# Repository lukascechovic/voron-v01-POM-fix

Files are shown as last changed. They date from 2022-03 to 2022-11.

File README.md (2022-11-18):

# voron-v01-POM-fix
**Issue: Z motor is binding/skipping at default 0.37A current with empty bed, with properly aligned parts (Z leadscrew and  POM nut T8_Nut_Block plastic part)**
[Youtube Video](https://youtu.be/tI24zk7298Q )

Originally used for LDO v0.1 kit rev C Anti Backlash Nut, POM, Tr8X8, if you got Z binding-skipping on default Z motor current 0.37A, with good Z axis alignment

hm.. increase in Z motor amps to 0.5A-0.55A solve this but at the cost of grinding plastic POM down and potentialy harm other parts of printer (head) as you really dont wanna super strong Z power (imagine Z endstop wont trigger)

**My best practice of aligning Z - before we hop into more unpleasant stuff**
1. fix Z motor (tighten all 4 screws) , bear in mind that you should trigger Z endstop with screw in T8_Nut_Block plastic part, for me it was more on rigth side from front view, POM nut is already on leadscrew
2. fix POM nut in T8_Nut_Block plastic part (tighten 2 screws), while T8_Nut_Block itself is still losen on alu Z profile
3. bring bed down (rotate leadscrew by hand), align T8_Nut_Block plastic part with leadscrew and tighten it (if you have backplate on, there are drilled two holes for wrench)
4. if you are lucky its working if not losen T8_Nut_Block plastic part and find better position.
5. if you are not able to find position without binding and you believe that you are doing everything rigth read next

**WHY this happenign to me?? - maybe spring on POM nut has thick wire, is short, with few "rings" which creating uneven pressure on POM nuts edge, this could create shear force locking nuts into leadscrew, it kills tolerance you need for other small missalignments which always occurs as there is NO way to have Z pefrectly squared**

**Solution1 - relieve spring tention with 3D printed spacer**

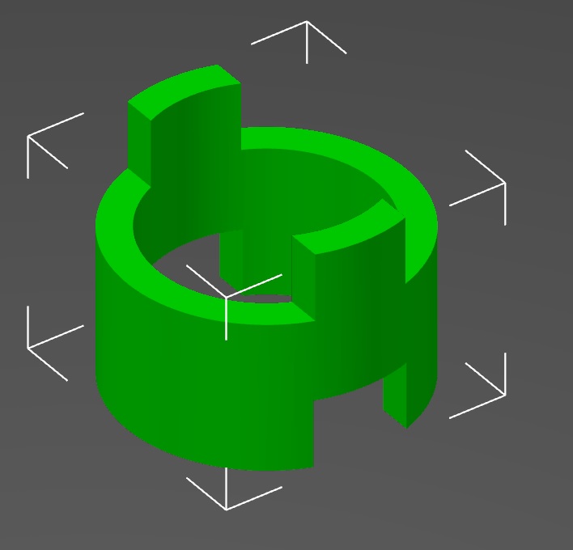
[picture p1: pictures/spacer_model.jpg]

 

**Solution2 - spring replacement, use spring with thinner wire and more rings**




Do not use brass nuts on ptfe coated LDO kits leadscrew, it grinds the leadscrew down.

**Solution3 - not use spring spring at all**
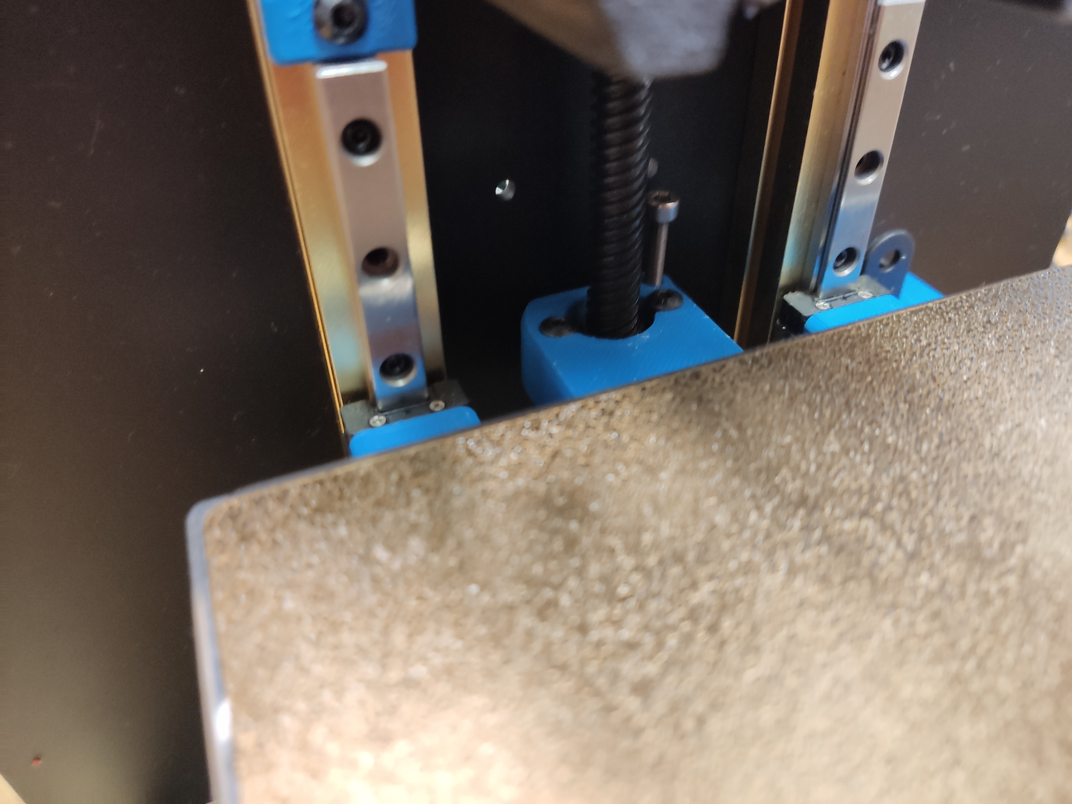
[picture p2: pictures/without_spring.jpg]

BTW this is solution I ended up with. It's hassle free solution. I just turned off Z-hops on travel moves to feel safer. I do not experience any problems with Z compare to my Voron v0.1 with spring.

**Conclusion**
With replacement spring or printed spacer or exclude spring and top part of nut from build its possible for example to move 180g cup up and down on default 0.37A on Z without skipping steps or binding.
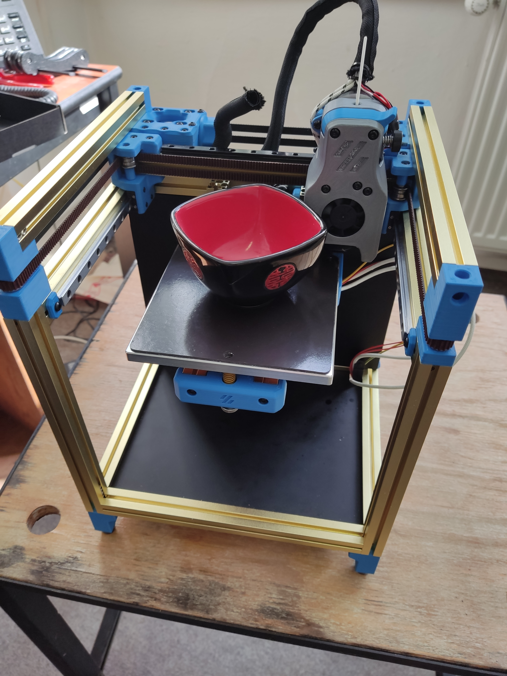
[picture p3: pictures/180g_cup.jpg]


It took me 4 whole days to solve this after two complete dissasemblies of printer as I was trying to square it. After spring replacement it worked on frist atttemp. Also printed spacer helped a lot with simmilar results.

**note 1**
I removed dragchain as I had feeling it is binding Z at the top position and I also feed cables from the bed under the bed, as gravity is helping with their binding

**note2**
I even tried to compensate T8_Nut_Block plastic part with bed drop... its 0.3 degree.. I remodeled it... printed... tested...
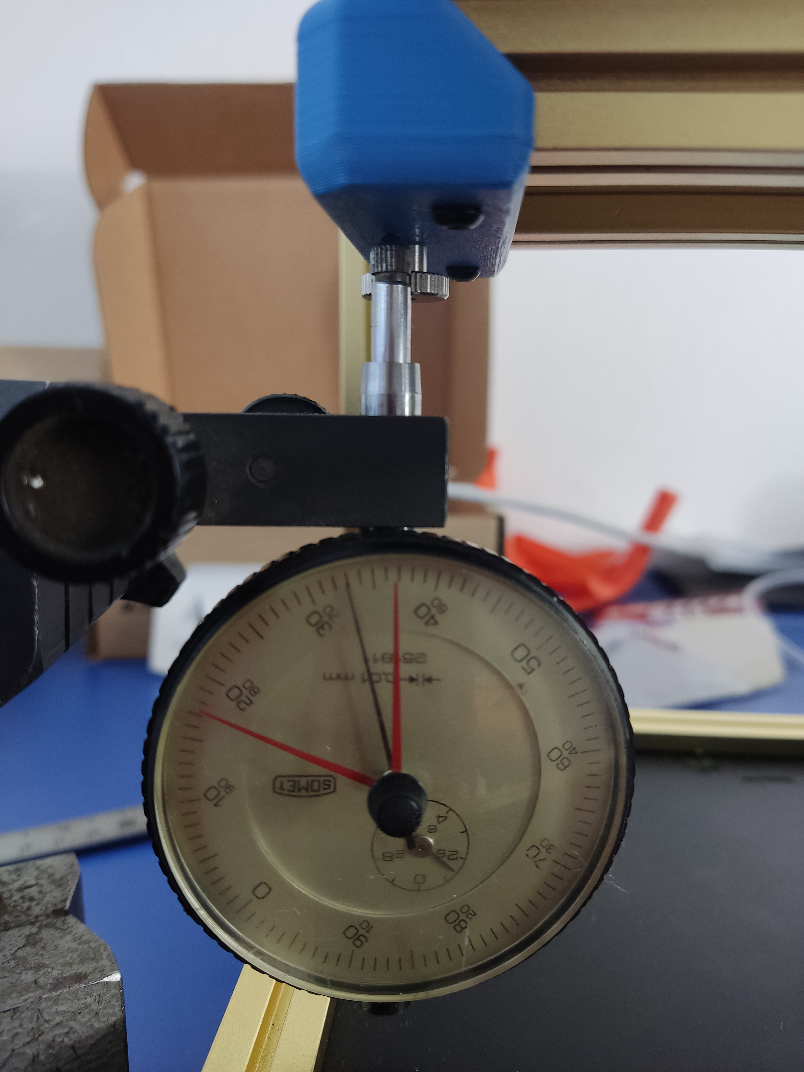
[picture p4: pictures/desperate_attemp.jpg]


one of two teardowns


**note 3**
On my second non-ldo kit voron v0.1 with non coated leadscrew I had not problems at all, Z working great with spring from start.
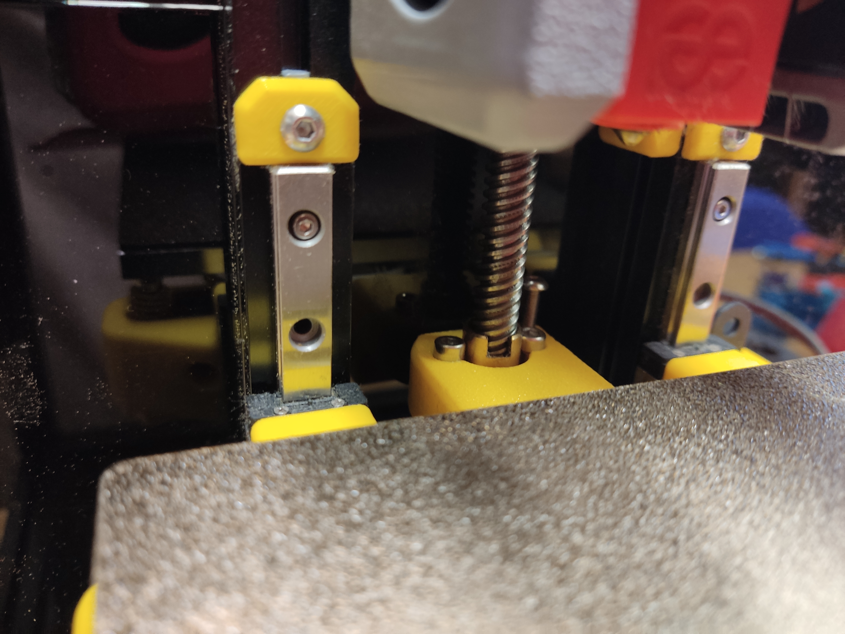
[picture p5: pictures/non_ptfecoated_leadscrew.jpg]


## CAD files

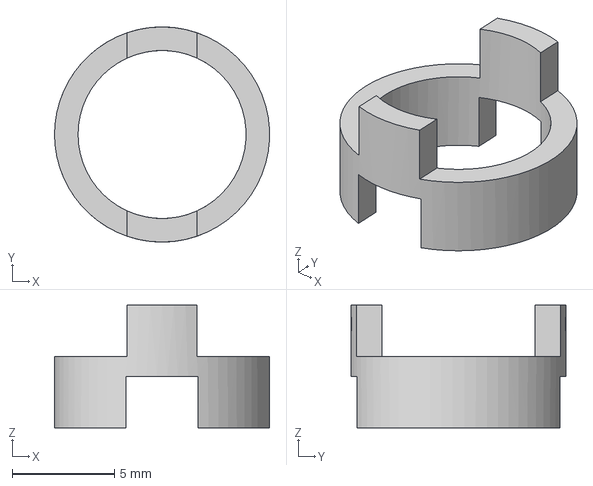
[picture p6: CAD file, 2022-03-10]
CAD files/spacer.step
10.5 x 10.5 x 6.00 mm

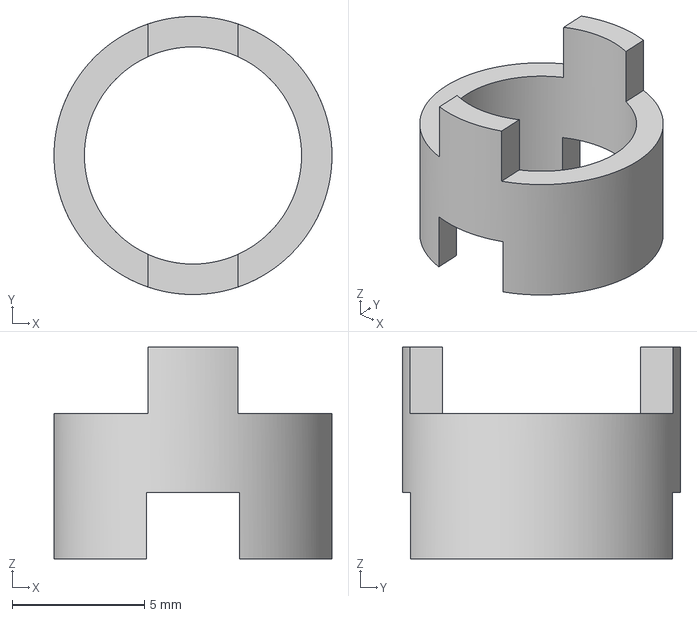
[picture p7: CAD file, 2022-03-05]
STL files/coupler.3mf
10.5 x 10.5 x 8.00 mm

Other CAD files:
CAD files/spacer v2.f3d
STL files/coupler.stl

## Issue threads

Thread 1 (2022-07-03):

Where is the difference?

diggit, 2022-07-03:
Hi,
I have V0.1 build from LDO kit manufactured in late 2021.
With every Z axis part from kit and 0.375 A motor current, I am pushing 400g tube of grease at full Z travel with boosted speed and acceleration:
```
max_z_velocity: 40
max_z_accel: 80
```
No issues.

The only difference I did was small change in assembly order.

At fist I mounted POM nut to plastic part of carriage, assembled whole Z axis and as the last step, mounted plastic part carrying nut to Z carriage extrusion.

In action...

https://user-images.githubusercontent.com/512025/177050641-d4f084af-8b62-4641-97a4-88202a234604.mp4

I am still not convinced, that any modifications are necessary. :shrug:

lukascechovic, 2022-11-18:
Hello, thx for message. Thats great your printer is working well. Whole Z assemble is done by mechanical engineers and its not imo suitable for reliable 3d printing. What I wanna say printed parts for Z plays huge role here (assemble too ofc) and you can end up with 3d pritned parts with slight deformation (non noticeable by eye) and using ptfe coated leadcrew with plastic nut takes away tolerance needed for those occasions. I have random v0.1 kit with non ptfe coated leadscrew with no problems at all from start. And yes most of people don't have problems but there was that time lots with problems. Even today another guy wrote me in search for solution. BR

Closed 2022-11-18.

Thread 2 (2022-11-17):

Spring Source

Aron3DP, 2022-11-17:
What replacement spring did you get and from where? I am going to test the spacer tonight and see how it works. I am having the same issue with my new build.

lukascechovic, 2022-11-18:
Hello, I just updated git with 3rd solution that is not use spring at all
which I ended up using. Spring was bought from random Czech eshop and it
was random chinese spring.

https://www.na3d.sk/p/3668/matica-na-trapezovu-skrutku-t8-t8x8-s-pruzinou

BR

št 17. 11. 2022 o 19:57 Aron ***@***.***> napísal(a):

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

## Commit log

2022-03-05 setting up
    [coupler.3mf, coupler.stl]
2022-03-10 Create spacer v2.f3d
    [spacer v2.f3d]
2022-03-10 Create spacer.step
    uploaded cad files
    [spacer.step]
